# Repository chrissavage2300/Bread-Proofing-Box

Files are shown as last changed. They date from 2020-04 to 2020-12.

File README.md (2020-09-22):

# Bread-Proofing-Box
A PID controlled bread proofing box with heater

<H3>Change log</H3>

<b>9/22/2020</b>After some consideration, I might just end up using a light bulb for a heater instead of the custom one. The one I wound by hand would be great for dehydrating stuff, but it would consume 600W! In open air, a 200W light bulb got pretty hot, so I think I may use a 40W to 60W bulb for such low temperatures. I dont know where else I could look for heater.

<b>9/19/2020</b> Output is now connected to the PID loop in code. After some minor adjustments on the bench, it seems to be working great!

<b>8/3/2020</b> Mile stone reached! I managed to dim a light after a few days worth of troubleshooting, I found out I needed a 4 Quad TRIAC. So the main TRIAC is now a BT138-600. I also had to change the output from timer 2 to stay low and then go high, essentially making this a constant off time circuit. Once I got that figured out, I then saw the proper sine waves!

<b>5/29/2020</b> Rotary Encoder Works. Timer 1 also works. Outputs also work. Waiting on Rev B.

<b>5/24/2020</b> A major error was found. The power IC's IC2 and 3 are backwards. I thought I fixed it from an older revision, but guess not. Either way the current board is a dud :(. Also the transformer doesnt fit either, so this is now in pause while I wait and do another PCB revision.

<b>5/11/2020</b> Added in documents to show heatsink calculations along with heater wire calculations

<b>5/11/2020</b> Idea: Timer function on screen, count down? Time Remaining. Have buzzer go off when "done". This would be useful for a hydrate function.

<b>5/08/2020</b>- Board sent to PCB maker.

<b>5/03/2020</b>-Initially started with a PIC16F15356 but realized that it may need more memory for running a glcd. Also may need more processing power and higher clock frequency's so I may go with a 18F26Q10. 

Also I may rethink the heater. It kind of smells like burning plastic when on, so I may design my own using Nichrome 60 wire

<b>4/28/2020</b>-Got mechanical encoder code working. Also stuck the heater in the box to get an idea of what kind of temps I could expect. It seemed to max out to around 114F and then the shutoff kicked in slightly after that. So the max temp should be around 120F. It took around 10 minutes to get up to this temp. Its not high enough for dehydration, but it is hot enough for bread making and yogurt making. Wonder how hot it would get if the over temp switch was bypassed. 

Display thoughts:
* Internal Temperature (°F)
* External Temperature (°F)
* Humidity (%)
* Run Time (HH:MM:SS)
* Set Temperature (°F)

More thoughts: I could use this box to dry soap.

Since I want to keep the integrity of the box, maybe I should mount the system on the top of the box. This way I can still use the box for storage when not in use. So have the heater fan on top and it can be a dual use fan for intake, and then have another fan on the opposite end on top for exhaust. 

<b>4/26/2020-Initial Idea</b>

Ideas/wants: Spawned from the sour dough book I have that talks about a storage box or a cooler along side a light to proof bread dough or proof sour dough starter. They use a light bulb, but my experience with bulbs is that they get pretty hot, almost to 90-100F. I only know this because I used them to start seeds as well. I had then begun to search around for heaters, initially I thought of winding my own using nichrome or kanthal wire, but deemed that too be unsafe as I could possibly touch it by accident.

Next I thought of using a cartridge heater, it could work but felt like it would be too inefficient. I finally settled on using just a small space heater. When this is done there is another added benefit: I can dehydrate food or make yogurt. I dont know yet what the lower and upper temperature bounds are of a 250W heater.

Features/Additions:
* A HDX 12 gallon storage bin is just big enough for the bowl I use and can fit a jar or two inside as well
* 250W 120VAC Heater from Walmart. Cant wait to take it apart! I have a suspicion its like the so called "100W 12V PTC heater" on ebay.
* I figure I'll add in an intake fan as well for cool or room temp air. Oh boy..if I wanted to cool the air that would be interesting. 
* Which suggests a dual PID of sorts. I dont have one PID working yet, but I have some code that might work thats unfinished. 
* PID 1 will control the heater
* Maybe have the heater fan run at 100% all the time and just be on/off control. 
  * Control Strategy
  1) PWM Will vary the heater to accommodate a set temperature.
  2) Heater Fan will Turn on or off depending on if its needed or not. So, if the heater is ramping up, the fan will come on. This suggests really long loop refresh times, maybe 10 seconds should be good. Its a small box.
  3) So if the box is at the set temperature, the heater will be at some value, and the fan will be circulating air pretty much. The heater doesnt need to be shut off in this case, but the duty cycle will be low probably. Maybe add in an input to shut the PID off but keep the fan on to circulate air? 
* Optional: Cool Air/Room temperature Air intake. Control scheme would probably be to turn on this fan if its get too hot and shut the heater off completely and just keep the recirculation fan running.   
* Complex Add on: 3D printed louver doors so heat isnt lost when the cooling fan isnt on. 
* Exhaust fan and intake fan. Heater fan will be the recirculation fan. 

IO List:
* Start Button
* Stop Button
* Quadrature Encoder Knob to select temperature
* Internal Analog Temperature (MCP 9700)
* External Analog Temperature
* Internal Analog Humidity
* Intake Fan-PWM or DO
* Exhaust Fan-DO
* Heater fan/Recirculation Fan-PWM or DO
* I2C Display, so 2 extra IO
* ZCD input to sync heater but this can be acommplished with extra circuitry too
* 32kHz Crystal for clock

Based on this, I would use one of the following PIC micro's
* PIC16F1773
* PIC16F15355
* ~~PIC18F24Q10~~
* ~~PIC18F24K40~~

The Box:
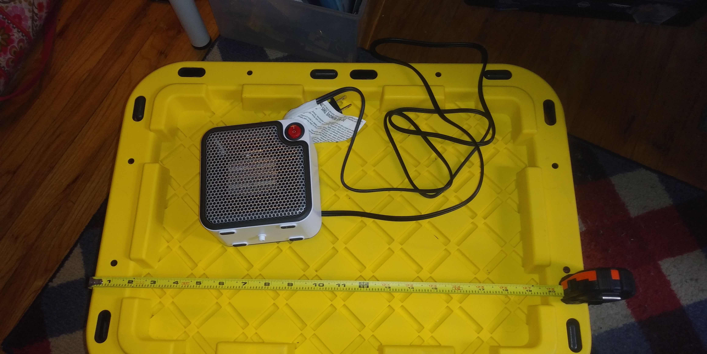
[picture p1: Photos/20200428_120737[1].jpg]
Box


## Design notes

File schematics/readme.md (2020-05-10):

Encoder adapter is an adapter to make it panel mountable. 

Page 1 and 2 have been seperated. Page 1 is the main board. Page 2 is the power.

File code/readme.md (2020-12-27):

Code Goes here.

Current working code is dated 2020_10_09_A

Possible future changes:

Remove Ambient Temp on  screen

Remove elapsed time on screen.

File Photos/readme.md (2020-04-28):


The box.
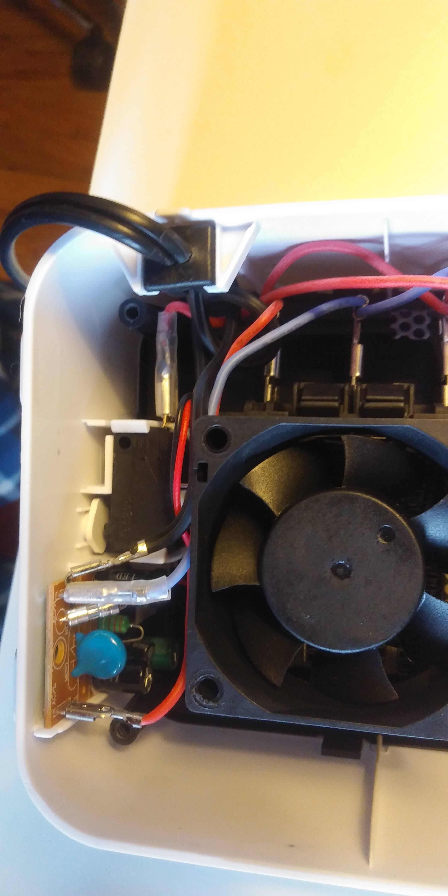
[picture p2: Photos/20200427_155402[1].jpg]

Fan looks pretty small, around 60mm I'd say. I probably wont need that big of a fan for the intake like I suspected.
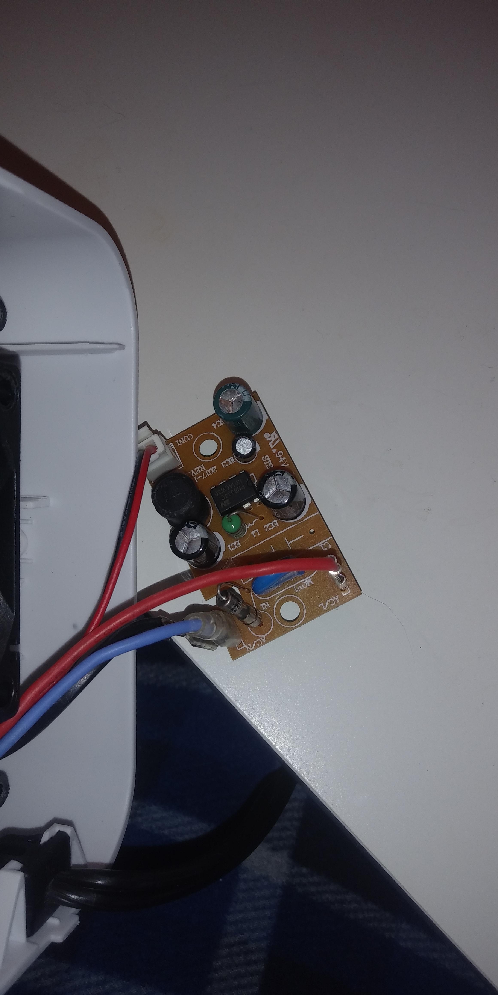
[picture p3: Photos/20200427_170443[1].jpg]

This seems to be some sort of buck SMPS. The datasheet I found suggests it puts out 12V, which confirms my initial suspicions that this is nothing more than those PTC heaters I found on ebay. I think I can use this to power my microcontroller circuit.
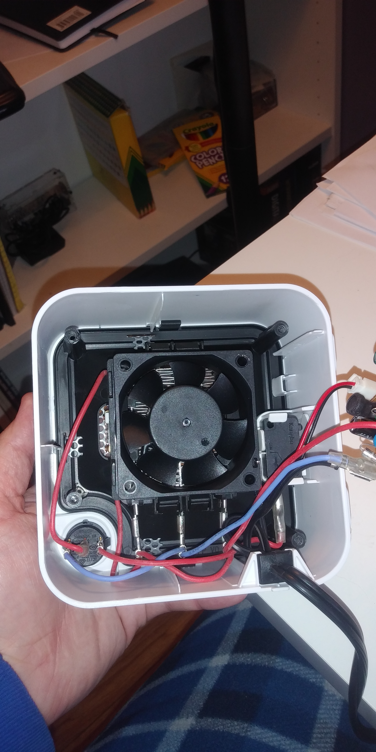
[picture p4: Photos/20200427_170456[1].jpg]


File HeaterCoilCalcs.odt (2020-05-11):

Heater Calculations

5 Coils, 4.8 each, 600W 24 total, connected in series
28AWG, Ni-60 0.32mm diameter
4.21 /ft

ID former = 0.25” or 6.350mm

5 each, 13.8inches long, 0.35m

Length of coil = {L times d times 1000} over {%pi times
(D+d)}
Where
L= wire length (0.35m)
d=0.32mm

D=6.350mm

d=0.32

Coil Length = 6.29mm or 0.75”

Stretch coil to certain length, 80mm

S = 80mm/6.29mm

S = 12 Wraps

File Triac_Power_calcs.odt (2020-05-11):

Triac Power Dissipation

I_{T (AVG)}= 2 times sqrt(2) times I_{RMS} over %pi

IRMS= 5A

IT (AVG) = 4.5A

P_TRIAC = V_{G T} times I_{T (AVG)} + RS times I_RMS

P_TRIAC = (1.5V times 4.5A) + (0.0316 times (5)^2)

P_TRIAC = 7.5W

TRIAC Heating

Heatsink selected: 4.7°C/W

T_J = Ambient Temp (°C) + P_{TRIAC}(W) times Thermal Resistance(°C/W)

T_J = 25°C + 7.5W times 4.7%°C/W

T_J = 25°C + 35.25°C

T_J = 60°C

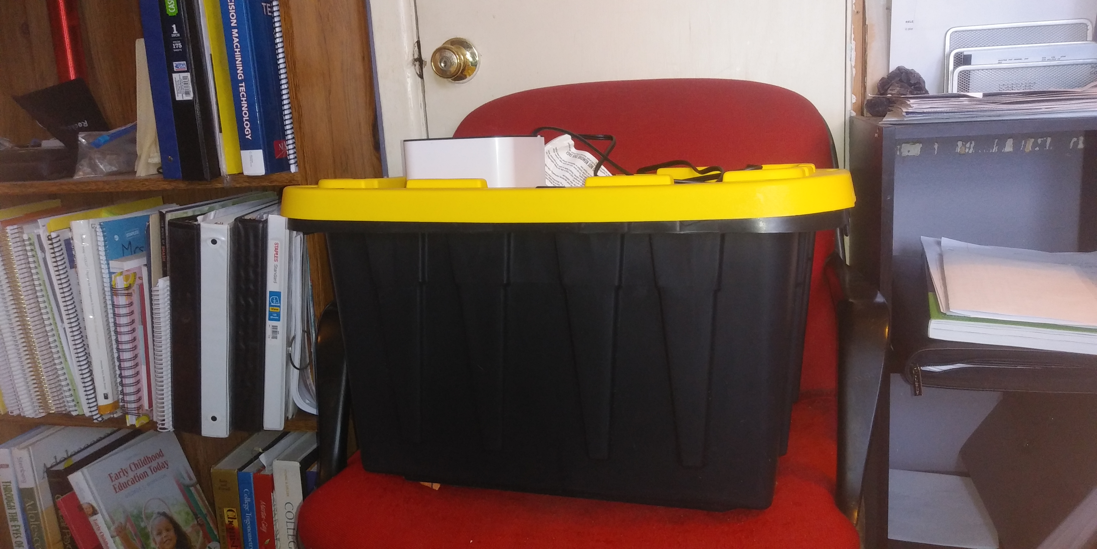
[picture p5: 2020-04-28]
Photos/20200428_120348[1].jpg

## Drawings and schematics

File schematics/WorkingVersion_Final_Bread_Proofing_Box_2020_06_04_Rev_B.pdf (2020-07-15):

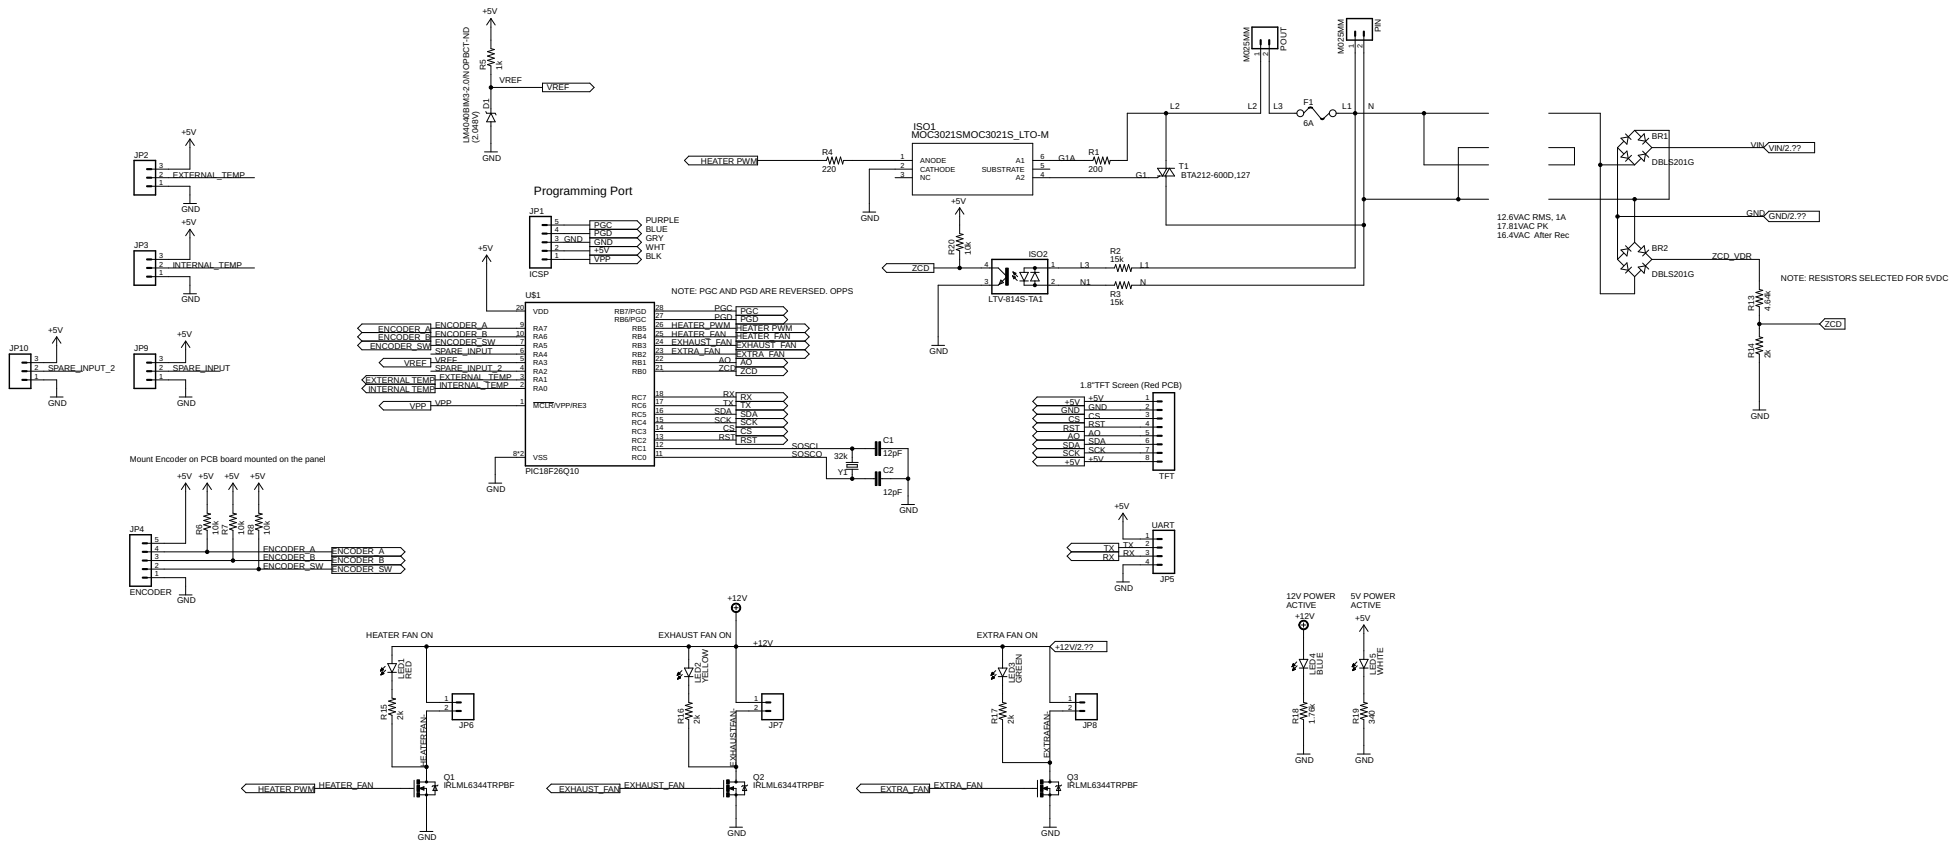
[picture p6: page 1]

PURPLE
BLUE GRY WHT BLK

NOTE: PGC AND PGD ARE REVERSED. OPPS

1.8"TFT Screen (Red PCB) Mount Encoder on PCB board mounted on the panel

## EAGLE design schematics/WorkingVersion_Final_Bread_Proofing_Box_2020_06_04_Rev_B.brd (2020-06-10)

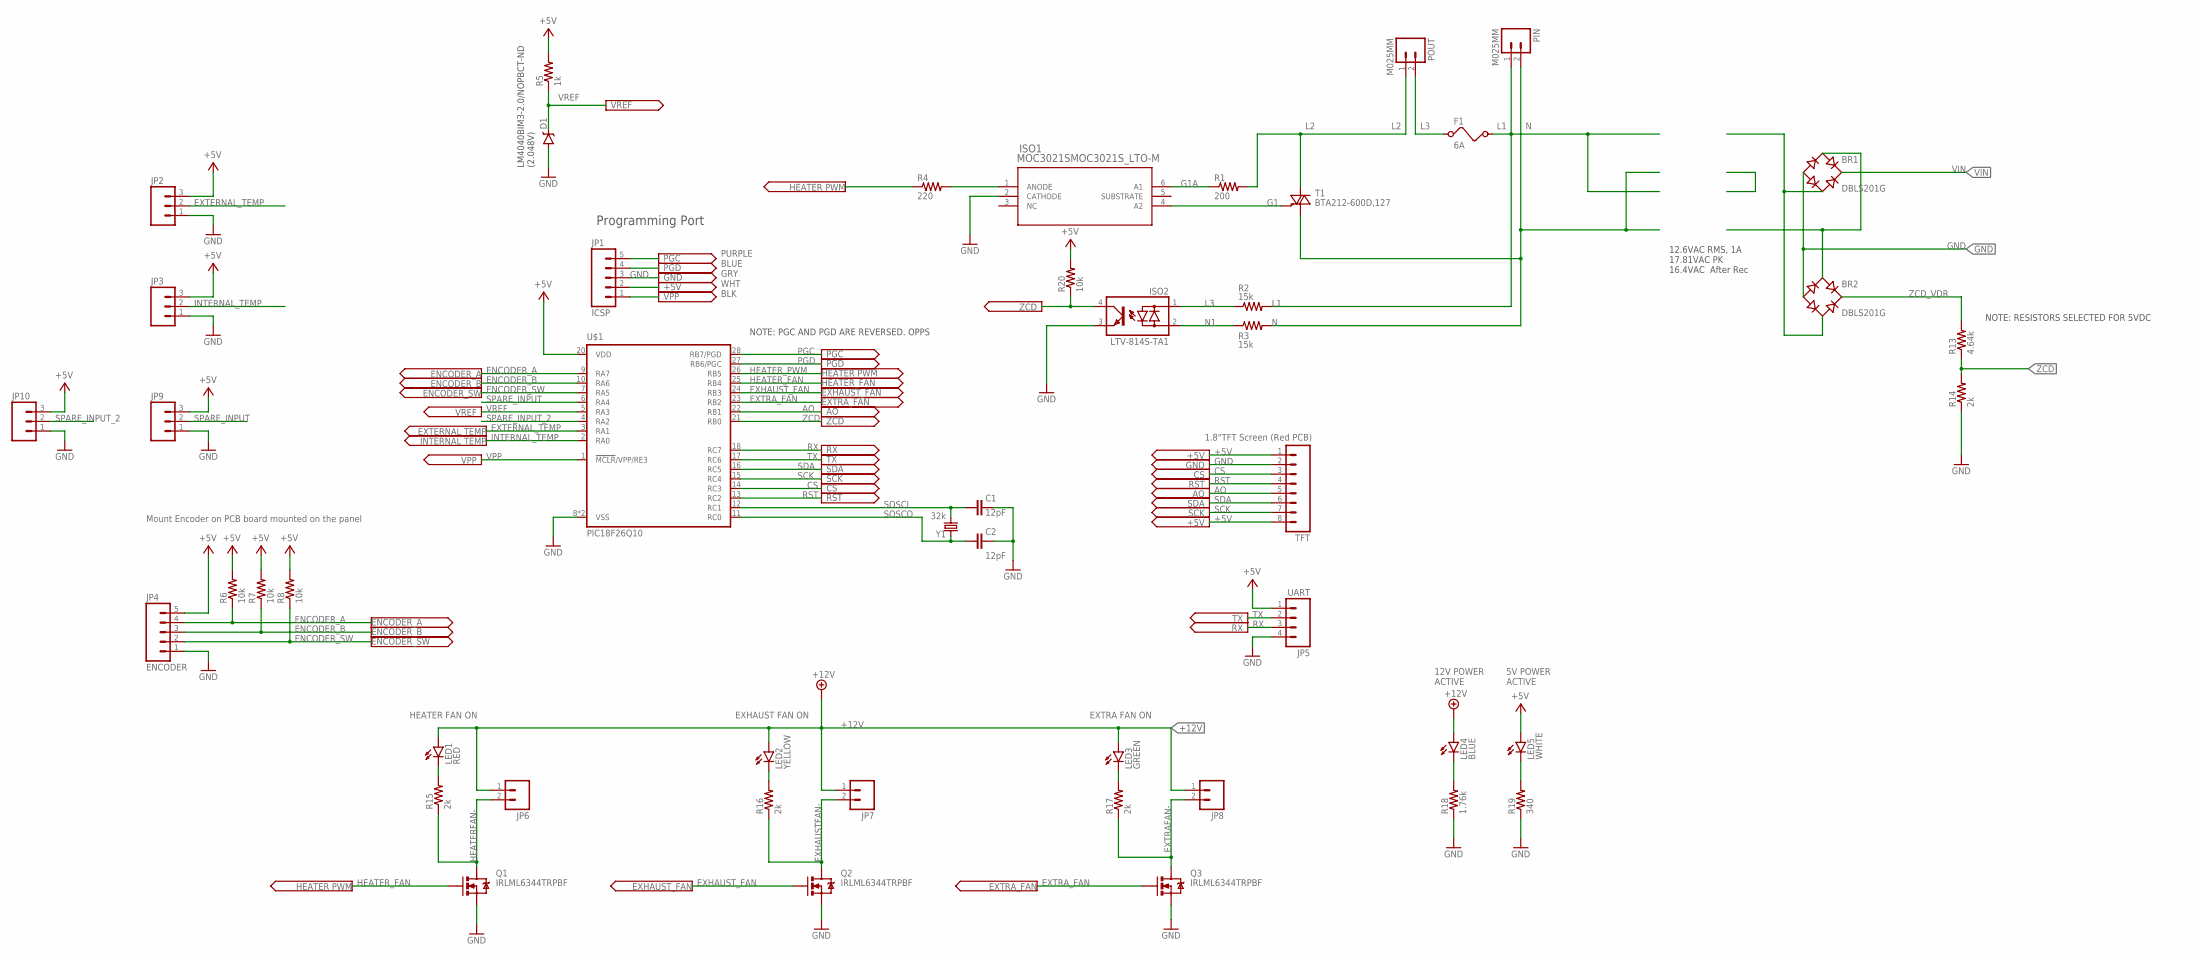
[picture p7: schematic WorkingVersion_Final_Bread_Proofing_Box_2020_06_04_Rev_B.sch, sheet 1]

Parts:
BR1, BR2: DBLS201G; DBS
C1, C2: 12pF; 0805
D1: V-REFERENCESMD; SOT23-3
F1: 6A; FUSE
ISO1: MOC3021SMOC3021S_LTO-M; MOC3021S_LTO-M
ISO2: LTV-814S-TA1; DIL4-SMD
JP1: ICSP; 1X05
JP2, JP3, JP9, JP10: M03POLAR; MOLEX-1X3
JP4: ENCODER; 1X05
JP5: UART; 1X04_LOCK
JP6, JP7, JP8: M02POLAR_LOCK; MOLEX-1X2_LOCK
LED1: RED; LED-1206
LED2: YELLOW; LED-1206
LED3: GREEN; LED-1206
LED4: BLUE; LED-1206
LED5: WHITE; LED-1206
PIN: M025MM; SCREWTERMINAL-5MM-2
POUT: M025MM; SCREWTERMINAL-5MM-2
Q1, Q2, Q3: IRLML6344TRPBF; SOT323
R1: 200; R2512
R2, R3: 15k; R2512
R4: 220; 1206
R5: 1k; 1206
R6, R7, R8, R20: 10k; 1206
R13: 4.64k; 1206
R14, R15, R16, R17: 2k; 1206
R18: 1.76k; 1206
R19: 340; 1206
T1: BTA212-600D,127; TO220BV
TFT: M08LOCK; 1X08_LOCK
U$1: PIC18F26Q10; SO28W
Y1: 32k; TC26V

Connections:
+5V: JP1.2, JP2.3, JP3.3, JP4.5, JP5.1, JP9.3, JP10.3, LED5.A, R5.2, R6.2, R7.2, R8.2, R20.2, TFT.1, TFT.8, U$1.20 (VDD); also elsewhere on the board
+12V: JP6.1, JP7.1, JP8.1, LED1.A, LED2.A, LED3.A, LED4.A; also elsewhere on the board
AO: TFT.5, U$1.22 (RB1)
CS: TFT.3, U$1.14 (RC3)
ENCODER_A: JP4.4, R6.1, U$1.9 (RA7)
ENCODER_B: JP4.3, R7.1, U$1.10 (RA6)
ENCODER_SW: JP4.2, R8.1, U$1.7 (RA5)
EXHAUSTFAN-: JP7.2, Q2.3 (D), R16.1
EXHAUST_FAN: Q2.1 (G), U$1.24 (RB3)
EXTERNAL_TEMP: JP2.2, U$1.3 (RA1)
EXTRAFAN-: JP8.2, Q3.3 (D), R17.1
EXTRA_FAN: Q3.1 (G), U$1.23 (RB2)
G1: ISO1.4 (A2), T1.G
G1A: ISO1.6 (A1), R1.1
GND: BR1.-, BR2.-, C1.2, C2.2, D1.2 (A), ISO1.2 (CATHODE), ISO2.3 (E), JP1.3, JP2.1, JP3.1, JP4.1, JP5.4, JP9.1, JP10.1, Q1.2 (S), Q2.2 (S), Q3.2 (S), R14.1, R18.1, R19.1, TFT.2, U$1.8 (VSS), U$1.19 (VSS); also elsewhere on the board
HEATERFAN-: JP6.2, Q1.3 (D), R15.1
HEATER_FAN: Q1.1 (G), U$1.25 (RB4)
HEATER_PWM: R4.1, U$1.26 (RB5)
INTERNAL_TEMP: JP3.2, U$1.2 (RA0)
L1: F1.2, PIN.1, R2.2
L2: POUT.1, R1.2, T1.T2 (A2)
L3: F1.1, ISO2.1 (AC1), POUT.2, R2.1
N: PIN.2, R3.2, T1.T1 (A1)
N1: ISO2.2 (AC2), R3.1
unnamed: ISO1.1 (ANODE), R4.2
unnamed: LED1.C, R15.2
unnamed: LED2.C, R16.2
unnamed: LED3.C, R17.2
unnamed: BR1.AC2, BR2.AC2
unnamed: BR1.AC1, BR2.AC1
unnamed: LED4.C, R18.2
unnamed: LED5.C, R19.2
PGC: JP1.5, U$1.28 (RB7/PGD)
PGD: JP1.4, U$1.27 (RB6/PGC)
RST: TFT.4, U$1.13 (RC2)
RX: JP5.3, U$1.18 (RC7)
SCK: TFT.7, U$1.15 (RC4)
SDA: TFT.6, U$1.16 (RC5)
SOSCI: C1.1, U$1.12 (RC1), Y1.1
SOSCO: C2.1, U$1.11 (RC0), Y1.2
SPARE_INPUT: JP9.2, U$1.6 (RA4)
SPARE_INPUT_2: JP10.2, U$1.4 (RA2)
TX: JP5.2, U$1.17 (RC6)
VIN: BR1.+; also elsewhere on the board
VPP: JP1.1, U$1.1 (!MCLR!/VPP/RE3)
VREF: D1.1 (C), R5.1, U$1.5 (RA3)
ZCD: ISO2.4 (C), R13.1, R14.2, R20.1, U$1.21 (RB0)
ZCD_VDR: BR2.+, R13.2

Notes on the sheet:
Programming Port
LM4040BIM3-2.0/NOPBCT-ND (2.048V)
1.8"TFT Screen (Red PCB)
12.6VAC RMS, 1A 17.81VAC PK 16.4VAC After Rec
Mount Encoder on PCB board mounted on the panel
12V POWER ACTIVE
5V POWER ACTIVE
HEATER FAN ON
EXHAUST FAN ON
EXTRA FAN ON
NOTE: RESISTORS SELECTED FOR 5VDC
NOTE: PGC AND PGD ARE REVERSED. OPPS
PURPLE BLUE GRY WHT BLK

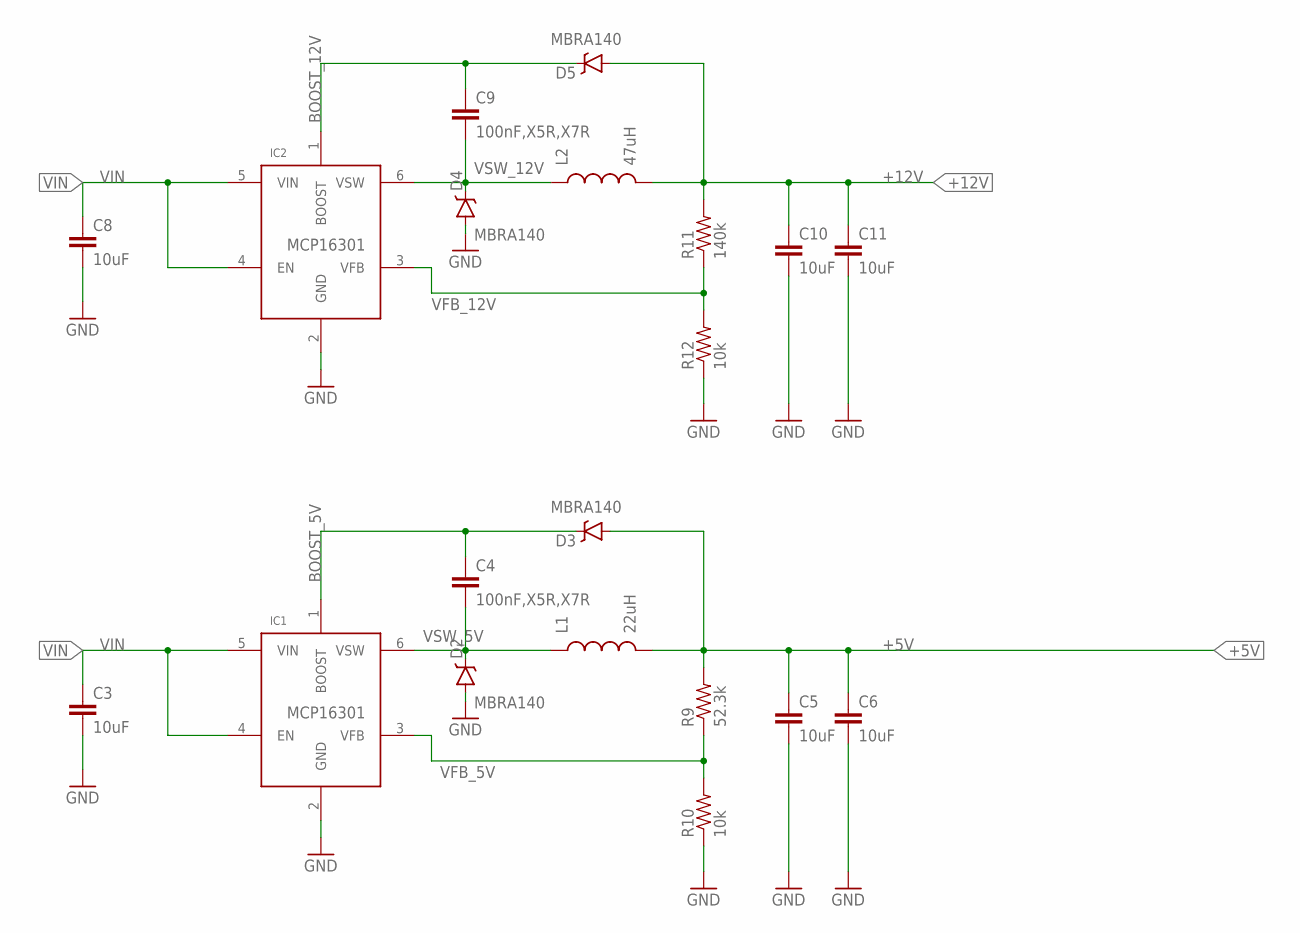
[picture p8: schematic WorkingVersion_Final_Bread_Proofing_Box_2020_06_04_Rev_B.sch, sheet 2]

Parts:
C3, C5, C6, C8, C10, C11: 10uF; 1206
C4, C9: 100nF,X5R,X7R; 1206
D2, D3, D4, D5: MBRA140; SMA-DIODE
IC1, IC2: MCP16301; SOT23-6
L1: 22uH; 1210
L2: 47uH; 1210
R9: 52.3k; 1206
R10, R12: 10k; 1206
R11: 140k; 1206

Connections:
+5V: C5.1, C6.1, D3.A, L1.2, R9.2; also elsewhere on the board
+12V: C10.1, C11.1, D5.A, L2.2, R11.2; also elsewhere on the board
BOOST_5V: C4.1, D3.C, IC1.1 (BOOST)
BOOST_12V: C9.1, D5.C, IC2.1 (BOOST)
GND: C3.2, C5.2, C6.2, C8.2, C10.2, C11.2, D2.A, D4.A, IC1.2 (GND), IC2.2 (GND), R10.1, R12.1; also elsewhere on the board
VFB_5V: IC1.3 (VFB), R9.1, R10.2
VFB_12V: IC2.3 (VFB), R11.1, R12.2
VIN: C3.1, C8.1, IC1.4 (EN), IC1.5 (VIN), IC2.4 (EN), IC2.5 (VIN); also elsewhere on the board
VSW_5V: C4.2, D2.C, IC1.6 (VSW), L1.1
VSW_12V: C9.2, D4.C, IC2.6 (VSW), L2.1

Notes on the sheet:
MCP16301

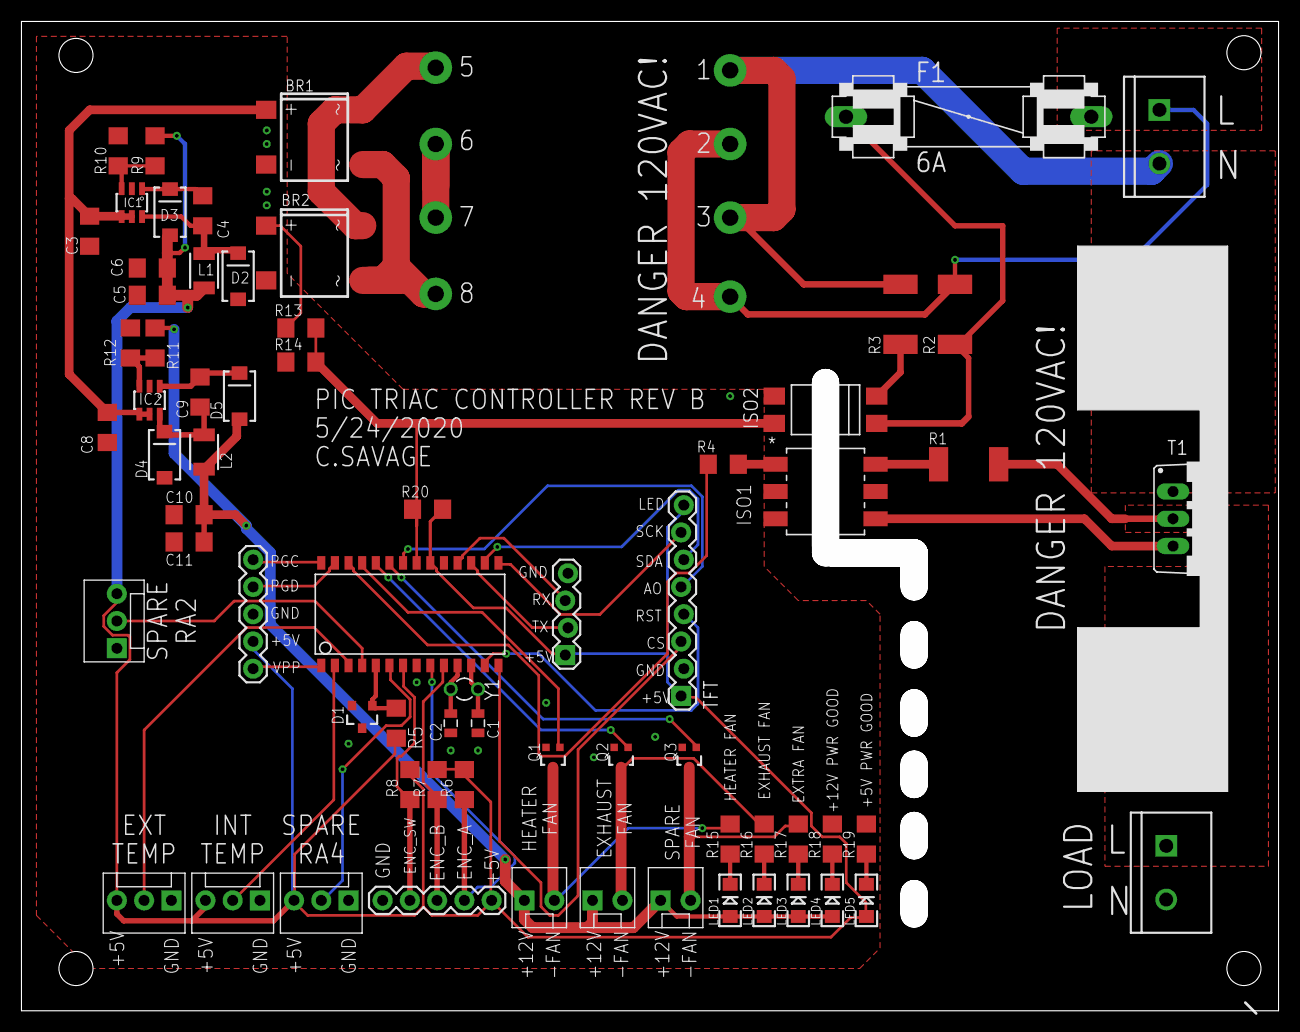
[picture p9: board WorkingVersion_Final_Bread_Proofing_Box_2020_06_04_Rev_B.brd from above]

Board: 2 copper layers, 117.1 x 92.2 mm, 69 parts (0 on the bottom side), 54 nets.

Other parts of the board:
HEATSINK: 7-345-2PP-BA

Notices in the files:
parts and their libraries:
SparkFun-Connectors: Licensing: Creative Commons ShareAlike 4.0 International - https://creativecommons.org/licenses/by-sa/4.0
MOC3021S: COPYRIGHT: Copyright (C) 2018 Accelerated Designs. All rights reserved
